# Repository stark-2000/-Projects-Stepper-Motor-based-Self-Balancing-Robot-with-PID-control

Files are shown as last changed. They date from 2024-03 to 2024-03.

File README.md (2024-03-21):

## Overview:
Developed a self-balancing robot using 𝘀𝘁𝗲𝗽𝗽𝗲𝗿 𝗺𝗼𝘁𝗼𝗿𝘀 and 𝗔𝟰𝟵𝟴𝟴 𝗱𝗿𝗶𝘃𝗲𝗿𝘀, driven by an Arduino-based 𝗣𝗜𝗗 balancing algorithm. Created a 𝗨𝗥𝗗𝗙 𝗺𝗼𝗱𝗲𝗹 and working towards 𝘁𝗲𝗹𝗲𝗼𝗽𝗲𝗿𝗮𝘁𝗶𝗼𝗻 from 𝗥𝗢𝗦.

## Key Achievements:
✦ 𝗦𝘁𝗲𝗽𝗽𝗲𝗿 𝗠𝗼𝘁𝗼𝗿 𝗜𝗻𝗻𝗼𝘃𝗮𝘁𝗶𝗼𝗻:
- Utilized stepper motors with A4988 drivers, 𝗲𝗹𝗶𝗺𝗶𝗻𝗮𝘁𝗶𝗻𝗴 the need for 𝗲𝗻𝗰𝗼𝗱𝗲𝗿𝘀 essential in DC motors, streamlining teleoperation prospects.

✦ 𝗘𝗳𝗳𝗶𝗰𝗶𝗲𝗻𝘁 𝗣𝗿𝗼𝘁𝗼𝘁𝘆𝗽𝗶𝗻𝗴:
- Leveraged SOLIDWORKS design and 3D printing for rapid prototyping, expediting development cycles for 𝘀𝘄𝗶𝗳𝘁 𝗶𝘁𝗲𝗿𝗮𝘁𝗶𝗼𝗻𝘀.

✦ 𝗖𝘂𝘀𝘁𝗼𝗺 𝗠𝗼𝘁𝗼𝗿 𝗖𝗼𝗻𝘁𝗿𝗼𝗹 𝗙𝘂𝗻𝗰𝘁𝗶𝗼𝗻:
- Wrote a custom function for stepper motor control via A4988 drivers, enhancing operational versatility 𝘄𝗶𝘁𝗵𝗼𝘂𝘁 the use of 𝗲𝘅𝗶𝘀𝘁𝗶𝗻𝗴 𝗹𝗶𝗯𝗿𝗮𝗿𝗶𝗲𝘀.

✦ 𝗕𝗮𝗹𝗮𝗻𝗰𝗶𝗻𝗴 𝗔𝗹𝗴𝗼𝗿𝗶𝘁𝗵𝗺 𝗜𝗺𝗽𝗹𝗲𝗺𝗲𝗻𝘁𝗮𝘁𝗶𝗼𝗻:
- Employed 𝗔𝗿𝗱𝘂𝗶𝗻𝗼'𝘀 𝗣𝗜𝗗 library for algorithmic balancing, ensuring stable and accurate self-balancing behavior of the robot.

✦ 𝗖𝘂𝘀𝘁𝗼𝗺 𝗣𝗖𝗕 𝗜𝗻𝘁𝗲𝗴𝗿𝗮𝘁𝗶𝗼𝗻:
- Designed a custom PCB integrating A4988 drivers, 𝗕𝗠𝗦 𝗰𝗶𝗿𝗰𝘂𝗶𝘁𝗿𝘆, 𝗕𝗡𝗢𝟬𝟱𝟱 𝗜𝗠𝗨, and 𝗟𝗶𝗣𝗼 battery, optimizing system 𝗲𝗳𝗳𝗶𝗰𝗶𝗲𝗻𝗰𝘆 and streamlining the functionality.

## Robot Pictures:



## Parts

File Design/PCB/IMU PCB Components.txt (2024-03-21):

IMU PCB:
Components:
BNO005 Module - 1

Connectors:
BNO005 Module:
6 pin male buck strip - 1 - IMU right side
4 pin male buck strip - 1 - IMU left side

Tracks:
All tracks - std tolerance

Other connector not on PCB:
6 pin female buck strip - 1 - IMU right side
4 pin female buck strip - 1 - IMU left side

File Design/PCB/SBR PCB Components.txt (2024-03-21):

Power PCB:
Components:
A4988 driver module - 2
lm2596 module - 1
lipo buzzer - 1

Connectors:
Battery:
2 pin JST male connector - 1 (high power - 3A to 5A max) - for LiPo

A4988:
4 pin male buck strip - 2 - for stepper motors 1A, 1B, 2A, 2B
2 pin male buck strip - 2 - for shorting slp & rst
4 pin male buck strip - 2 - for MS1, 2, 3, and enable 
2 pin male buck strip - 2 - for Step, Dir

LM2596S:
2 pin male buck strip - 1 - for RPi power supply

LiPo Buzzer:
9 pin female buck strip 90° bent - 1 - for LiPo buzzer

Tracks:
Stepper tracks 1A, 1B, 2A, 2B - 1.5A tolerance
JST to A4988 & LM2596 IN - 5A max tolerance
All other tracks - std tolerance

Other connector not on PCB Layout:
1 pin female buck strip - 4 - for LM2596S
8 pin female buck strip - 4 - for A4988

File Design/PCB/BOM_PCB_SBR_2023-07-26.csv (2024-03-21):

ID | Name | Designator | Footprint | Quantity | Manufacturer Part | Manufacturer | Supplier | Supplier Part | Price
1 | Header-Male-2.54_1x4 | M1,MS1,M2,MS2 | HDR-TH_4P-P2.54-V-M | 4 | 210S-1*4P L=11.6MMGold-plated black | Ckmtw | LCSC | C124378 | 0.042
2 | 2.54mm 1*2P | P1_5V,SLP1,SD1,SLP2,SD2 | HDR-TH_2P-P2.54-V-M | 5 | 2.54mm 1*2P | ReliaPro | LCSC | C36717 | 0.006
3 | LM2596-DC-DC-module | U1 | LM2596-DC-DC-MODULE | 1
4 | 2.54mm 1*9P Male | H9 | HDR-TH_9P-P2.54-V-M | 1
5 | 2.54mm 1*2P JST | P2_11V | CONN-TH_M2545V-02P | 1
6 | 2.54mm 1*9P Female | U4 | HDR-TH_9P-P2.54-H-F-W10.0-N | 1
7 | A4988 | U3,U2 | A4988 | 2 | A4988 1

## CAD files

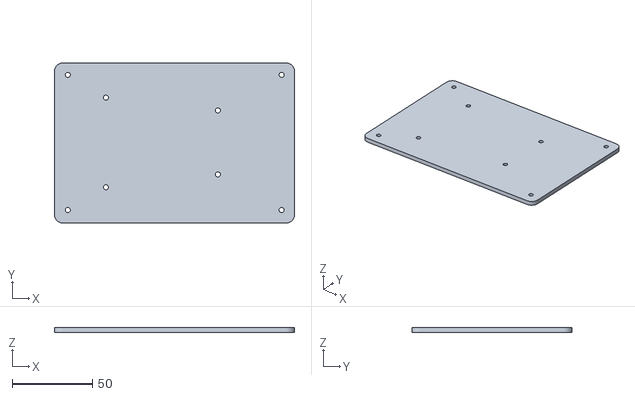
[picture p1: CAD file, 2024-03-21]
3D Print Files/SBR_Top_Rack.stl
150.0 x 100.0 x 3.00

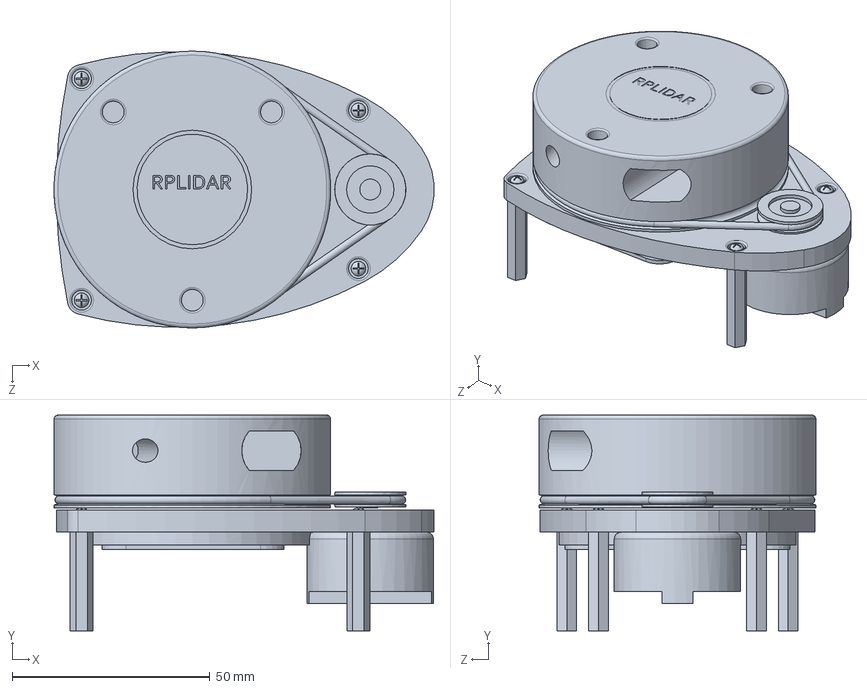
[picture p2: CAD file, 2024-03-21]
Design/CAD/Step Files/RPLidar.SLDPRT
96.1 x 54.6 x 70.0 mm

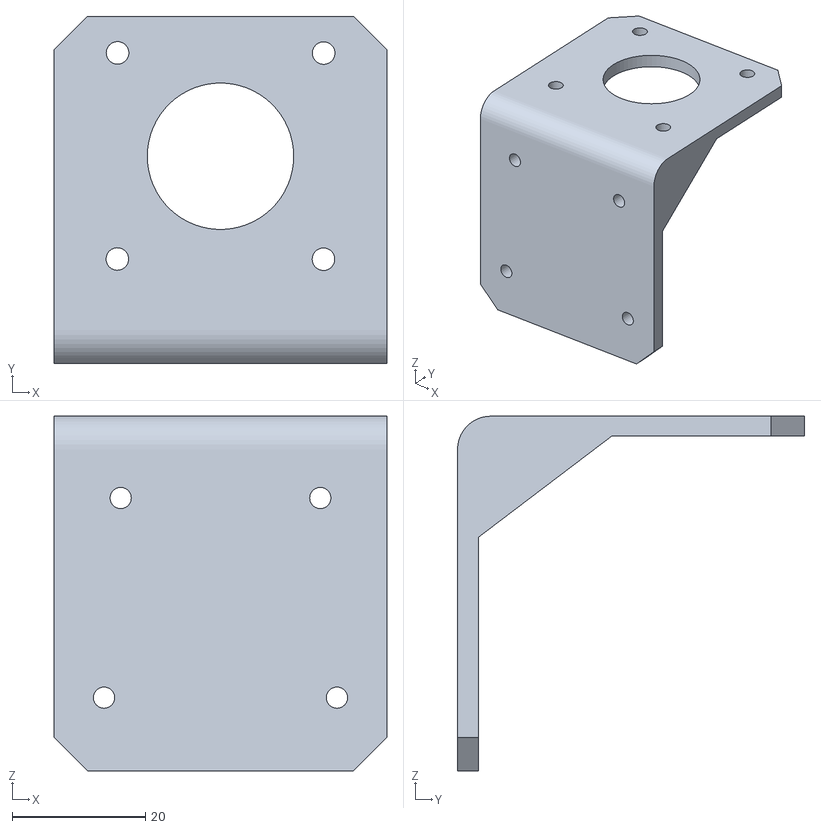
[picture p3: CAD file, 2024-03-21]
3D Print Files/Nema17_Bracket.stl
50.0 x 52.1 x 53.3

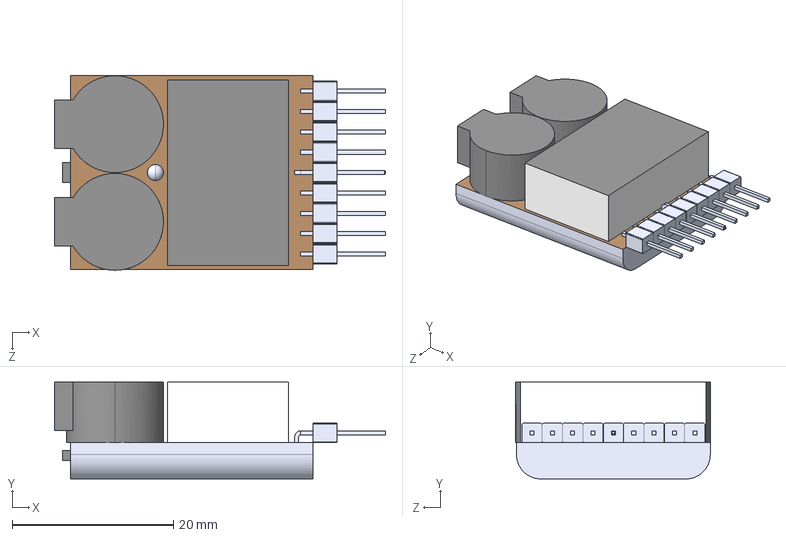
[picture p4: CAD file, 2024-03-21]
Design/CAD/Step Files/LiPo Alarm.STEP
41.0 x 12.0 x 24.1 mm

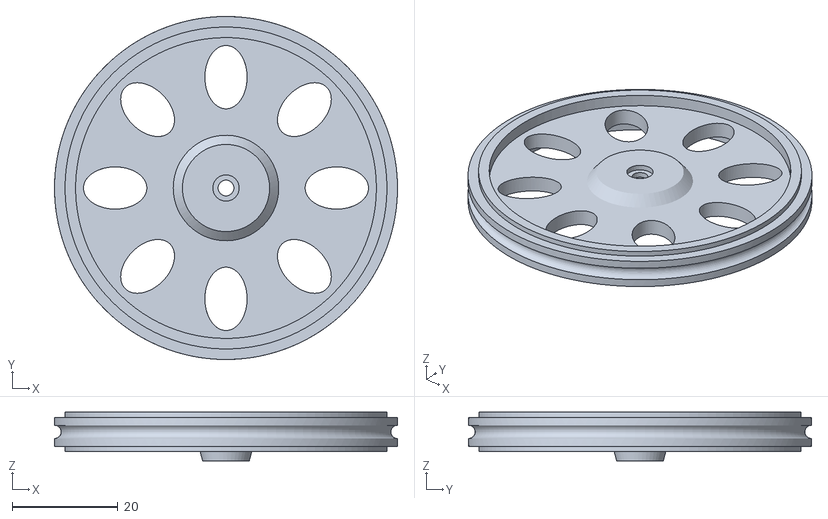
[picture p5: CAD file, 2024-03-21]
3D Print Files/Wheel_SBR.stl
65.0 x 65.0 x 9.25

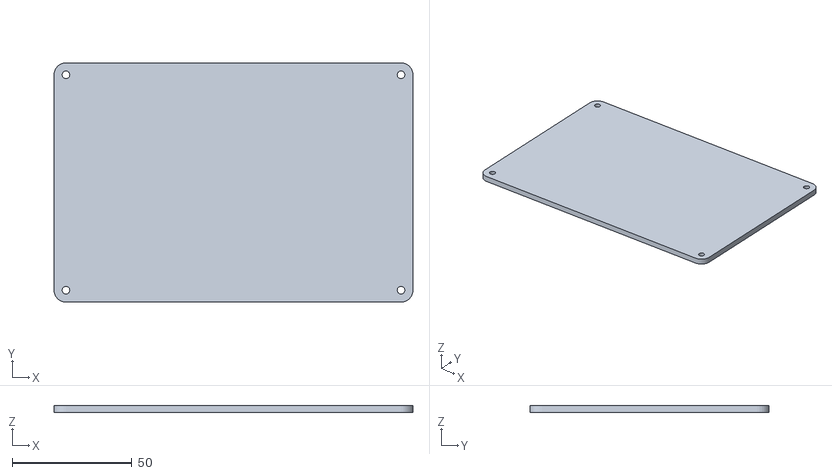
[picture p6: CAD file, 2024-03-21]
3D Print Files/SBR_Middle_Rack.stl
150.0 x 100.0 x 3.00

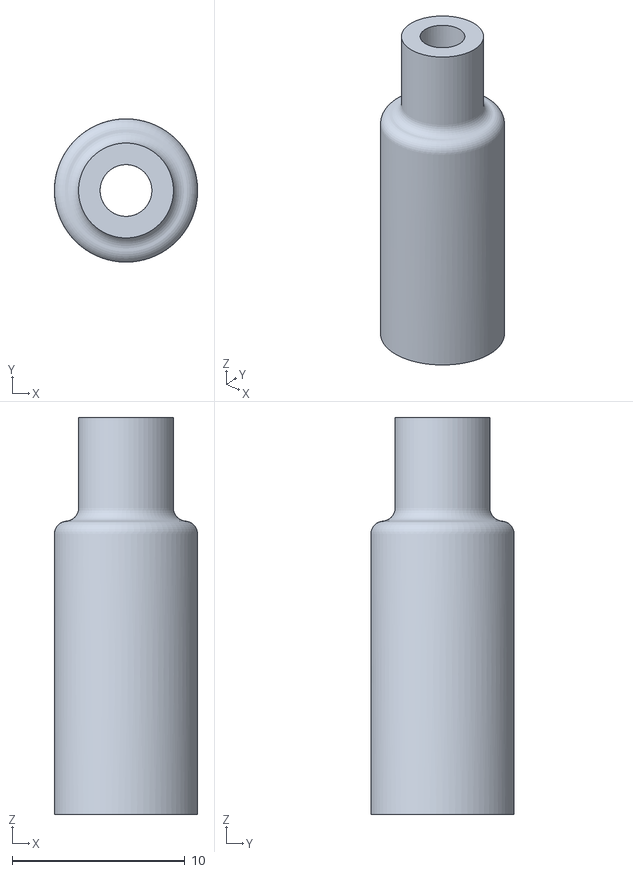
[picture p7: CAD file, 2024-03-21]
3D Print Files/Stepper_Coupler_2.stl
8.30 x 8.30 x 23.0

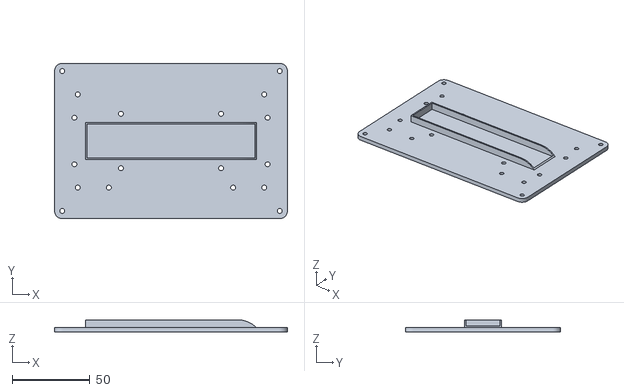
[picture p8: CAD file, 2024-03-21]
3D Print Files/SBR_Bottom_Rack.stl
150.0 x 100.0 x 8.00

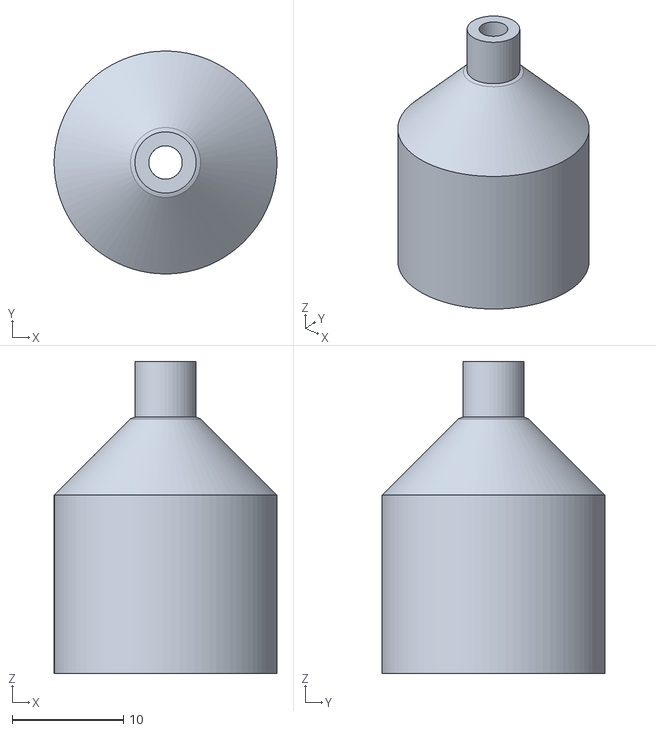
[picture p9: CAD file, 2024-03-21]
3D Print Files/Stepper_Coupler_3.stl
20.0 x 20.0 x 28.0

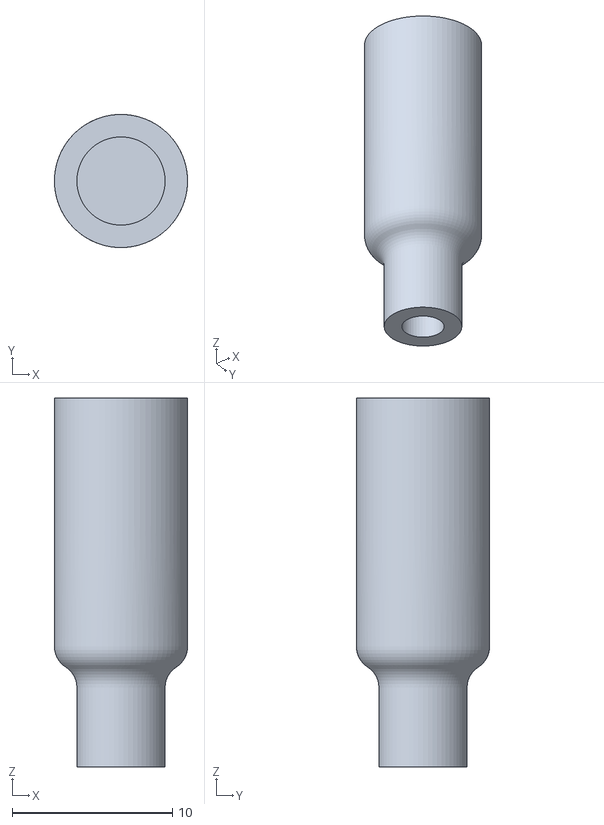
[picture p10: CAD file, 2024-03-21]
3D Print Files/Stepper_Coupler_1.stl
8.30 x 8.30 x 23.0

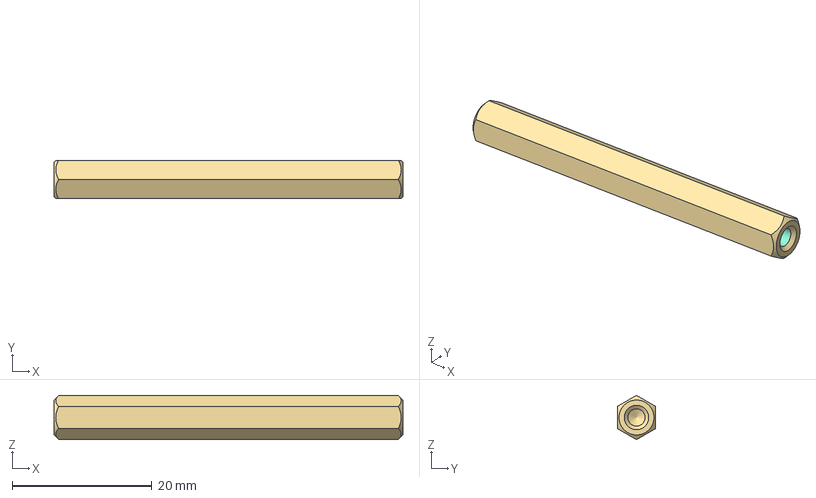
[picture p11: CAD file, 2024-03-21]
Design/CAD/Step Files/M3 50mm Stud_Spacer.stp
50.0 x 5.50 x 6.35 mm

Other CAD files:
Design/CAD/Step Files/NEMA_17_Bracket.stp

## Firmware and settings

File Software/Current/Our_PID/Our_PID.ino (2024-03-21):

//////////////////////////////////////////////////////////////////
//PID Interface:
#include <PID_v1.h> //From https://github.com/br3ttb/Arduino-PID-Library/blob/master/PID_v1.h

/*********Tune these 4 values for your BOT*********/

double setpoint= 88; //set the value when the bot is perpendicular to ground using serial monitor. 

//Read the project documentation on circuitdigest.com to learn how to set these values
double Kp = 21; //Set this first
double Kd = 0.8; //Set this secound
double Ki = 140; //Finally set this 

/******End of values setting*********/

double input, output;
PID pid(&input, &output, &setpoint, Kp, Ki, Kd, DIRECT);

//////////////////////////////////////////////////////////////////

//////////////////////////////////////////////////////////////////
//IMU Interface:
#include <SoftwareSerial.h>
int RXPin = 6; //Connect TX of GPS to Pin 2
int TXPin = 7; //Connect RX of GPS to Pin 3
SoftwareSerial nanoSerial(RXPin, TXPin);

//////////////////////////////////////////////////////////////////

//////////////////////////////////////////////////////////////////
//Stepper Interface:
//Defines pins numbers
const int dirPin1 = 3;
const int stepPin1 = 2;

const int dirPin2 = 5;
const int stepPin2 = 4;

//////////////////////////////////////////////////////////////////


void setup() {
  Serial.begin(9600);

  Serial.println("Intialising IMU Serial interface..."); 
  nanoSerial.begin(9600);

  //Stepper Initialisation:
  Serial.println("Intialising Stepper Motor..."); 
  pinMode(stepPin1,OUTPUT);
  pinMode(dirPin1,OUTPUT);
  pinMode(stepPin2,OUTPUT);
  pinMode(dirPin2,OUTPUT);
}


void loop() {
  // int data = nanoSerial.read();
  while (nanoSerial.available() > 0){
    // input = data * 180/M_PI + 180;
    input = nanoSerial.read();
    
    //no mpu data - performing PID calculations and output to motors     
    pid.Compute();   

    //Print the value of Input and Output on serial monitor to check how it is working.
    Serial.print(input); Serial.print(" =>"); Serial.println(output);

    if (input>60 && input<110){//If the Bot is falling 
      if (output>0){ //Falling towards front 
        int speed = map(output, 0, 255, 40000, 100);
        Forward(speed); //Rotate the wheels forward 
      }

      else if (output<0){ //Falling towards back
        int speed = map(output, 0, 255, 40000, 100);
        Reverse(speed); //Rotate the wheels backward 
      }
    }

    else //If Bot not falling
      Stop(); //Hold the wheels still

  }
}



void Forward(int intervalBetweenSteps){
  digitalWrite(dirPin1,HIGH);
  digitalWrite(dirPin2,LOW);

  digitalWrite(stepPin1, HIGH);
  delayMicroseconds(5); //this is the pulse width - trigger
  digitalWrite(stepPin1, LOW);
  delayMicroseconds(intervalBetweenSteps);

  digitalWrite(stepPin2, HIGH);
  delayMicroseconds(5); //this is the pulse width - trigger
  digitalWrite(stepPin2, LOW);
  delayMicroseconds(intervalBetweenSteps);
}


void Reverse(int intervalBetweenSteps){
  digitalWrite(dirPin1,LOW);
  digitalWrite(dirPin2,HIGH);

  digitalWrite(stepPin1, HIGH);
  delayMicroseconds(5); //this is the pulse width - trigger
  digitalWrite(stepPin1, LOW);
  delayMicroseconds(intervalBetweenSteps * -1);

  digitalWrite(stepPin2, HIGH);
  delayMicroseconds(5); //this is the pulse width - trigger
  digitalWrite(stepPin2, LOW);
  delayMicroseconds(intervalBetweenSteps * -1);
}


void Stop(){
  digitalWrite(stepPin1, LOW);
  digitalWrite(stepPin2, LOW);
}

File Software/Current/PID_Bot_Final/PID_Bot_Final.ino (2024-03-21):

#include "I2Cdev.h"
#include <PID_v1.h> //From https://github.com/br3ttb/Arduino-PID-Library/blob/master/PID_v1.h
#include "MPU6050_6Axis_MotionApps20.h" //https://github.com/jrowberg/i2cdevlib/tree/master/Arduino/MPU6050

MPU6050 mpu;

// MPU control/status vars
bool dmpReady = false;  // set true if DMP init was successful
uint8_t mpuIntStatus;   // holds actual interrupt status byte from MPU
uint8_t devStatus;      // return status after each device operation (0 = success, !0 = error)
uint16_t packetSize;    // expected DMP packet size (default is 42 bytes)
uint16_t fifoCount;     // count of all bytes currently in FIFO
uint8_t fifoBuffer[64]; // FIFO storage buffer

// orientation/motion vars
Quaternion q;           // [w, x, y, z]         quaternion container
VectorFloat gravity;    // [x, y, z]            gravity vector
float ypr[3];           // [yaw, pitch, roll]   yaw/pitch/roll container and gravity vector

/*********Tune these 4 values for your BOT*********/

double setpoint= 176; //set the value when the bot is perpendicular to ground using serial monitor. 

//Read the project documentation on circuitdigest.com to learn how to set these values
double Kp = 21; //Set this first
double Kd = 0.8; //Set this secound
double Ki = 140; //Finally set this 

/******End of values setting*********/



double input, output;

PID pid(&input, &output, &setpoint, Kp, Ki, Kd, DIRECT);

volatile bool mpuInterrupt = false;     // indicates whether MPU interrupt pin has gone high

void dmpDataReady()
{
  mpuInterrupt = true;
}


void setup() {
  Serial.begin(115200);

  // initialize device
    Serial.println(F("Initializing I2C devices..."));
    mpu.initialize();

    // verify connection
    Serial.println(F("Testing device connections..."));
    Serial.println(mpu.testConnection() ? F("MPU6050 connection successful") : F("MPU6050 connection failed"));

    // load and configure the DMP
    devStatus = mpu.dmpInitialize();

    // supply your own gyro offsets here, scaled for min sensitivity
    mpu.setXGyroOffset(220);
    mpu.setYGyroOffset(76);
    mpu.setZGyroOffset(-85);
    mpu.setZAccelOffset(1688); 

    // make sure it worked (returns 0 if so)
    if (devStatus == 0)
    {
        // turn on the DMP, now that it's ready
        Serial.println(F("Enabling DMP..."));
        mpu.setDMPEnabled(true);

        // enable Arduino interrupt detection
        Serial.println(F("Enabling interrupt detection (Arduino external interrupt 0)..."));
        attachInterrupt(0, dmpDataReady, RISING);
        mpuIntStatus = mpu.getIntStatus();

        // set our DMP Ready flag so the main loop() function knows it's okay to use it
        Serial.println(F("DMP ready! Waiting for first interrupt..."));
        dmpReady = true;

        // get expected DMP packet size for later comparison
        packetSize = mpu.dmpGetFIFOPacketSize();

        //setup PID
        pid.SetMode(AUTOMATIC);
        pid.SetSampleTime(10);
        pid.SetOutputLimits(-255, 255);  

    }

    else
    {
        // ERROR!
        // 1 = initial memory load failed
        // 2 = DMP configuration updates failed
        // (if it's going to break, usually the code will be 1)

        Serial.print(F("DMP Initialization failed (code "));
        Serial.print(devStatus);
        Serial.println(F(")"));
    }


//Initialise the Motor outpu pins
    pinMode (6, OUTPUT);
    pinMode (9, OUTPUT);
    pinMode (10, OUTPUT);
    pinMode (11, OUTPUT);

//By default turn off both the motors
    analogWrite(6,LOW);
    analogWrite(9,LOW);
    analogWrite(10,LOW);
    analogWrite(11,LOW);
}


void loop() {
    // if programming failed, don't try to do anything
    if (!dmpReady) return;

    // wait for MPU interrupt or extra packet(s) available
    while (!mpuInterrupt && fifoCount < packetSize)
    {
        //no mpu data - performing PID calculations and output to motors     
        pid.Compute();   

        //Print the value of Input and Output on serial monitor to check how it is working.
        Serial.print(input); Serial.print(" =>"); Serial.println(output);

        if (input>150 && input<200){//If the Bot is falling 
          if (output>0) //Falling towards front 
            Forward(); //Rotate the wheels forward 

          else if (output<0) //Falling towards back
            Reverse(); //Rotate the wheels backward 
        }

        else //If Bot not falling
          Stop(); //Hold the wheels still
    }

    // reset interrupt flag and get INT_STATUS byte
    mpuInterrupt = false;
    mpuIntStatus = mpu.getIntStatus();

    // get current FIFO count
    fifoCount = mpu.getFIFOCount();

    // check for overflow (this should never happen unless our code is too inefficient)
    if ((mpuIntStatus & 0x10) || fifoCount == 1024)
    {
        // reset so we can continue cleanly
        mpu.resetFIFO();
        Serial.println(F("FIFO overflow!"));

    // otherwise, check for DMP data ready interrupt (this should happen frequently)
    }

    else if (mpuIntStatus & 0x02)
    {
        // wait for correct available data length, should be a VERY short wait
        while (fifoCount < packetSize) fifoCount = mpu.getFIFOCount();

        // read a packet from FIFO
        mpu.getFIFOBytes(fifoBuffer, packetSize);

        // track FIFO count here in case there is > 1 packet available
        // (this lets us immediately read more without waiting for an interrupt)
        fifoCount -= packetSize;

        mpu.dmpGetQuaternion(&q, fifoBuffer); //get value for q
        mpu.dmpGetGravity(&gravity, &q); //get value for gravity
        mpu.dmpGetYawPitchRoll(ypr, &q, &gravity); //get value for ypr

        input = ypr[1] * 180/M_PI + 180;
   }

}


void Forward() //Code to rotate the wheel forward 
{
    analogWrite(6,output);
    analogWrite(9,0);
    analogWrite(10,output);
    analogWrite(11,0);
    Serial.print("F"); //Debugging information 
}


void Reverse() //Code to rotate the wheel Backward  
{
    analogWrite(6,0);
    analogWrite(9,output*-1);
    analogWrite(10,0);
    analogWrite(11,output*-1); 
    Serial.print("R");
}


void Stop() //Code to stop both the wheels
{
    analogWrite(6,0);
    analogWrite(9,0);
    analogWrite(10,0);
    analogWrite(11,0); 
    Serial.print("S");
}

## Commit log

2024-03-21 Mechanical & Electronic Architecture update
    [BOM_PCB_SBR_2023-07-26.csv, LiPo Alarm.STEP, M3 50mm Stud_Spacer.stp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]
2024-03-21 Software Stack PID update
2024-03-21 3D Print STL
    [Nema17_Bracket.stl, SBR_Bottom_Rack.stl, SBR_Middle_Rack.stl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]
